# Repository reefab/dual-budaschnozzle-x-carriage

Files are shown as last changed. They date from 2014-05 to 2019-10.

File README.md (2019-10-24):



Dual-Budaschnozzle-X-Carriage
=============================

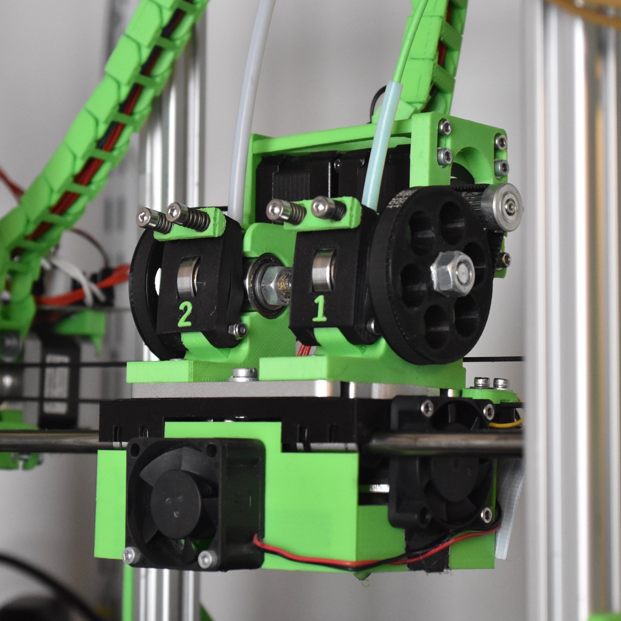
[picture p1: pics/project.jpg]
Assembled

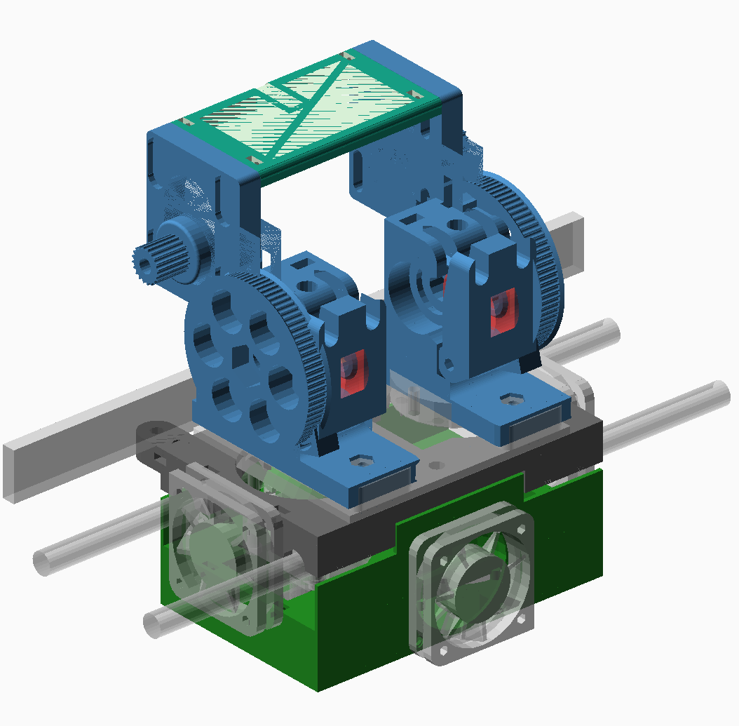
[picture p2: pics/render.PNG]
Final picture


A combination of X-carriage (black), extruders (blue), and fanduct/thermal shield (green) for the [Geetech Dual-head Hotend](http://www.geeetech.com/dualhead-hotend-extruder-0350405mm-nozzle-for-3mm-filament-p-749.html) which uses two budaschnozzles.

Made for Mendel-style horizontal X-axis printers. Has emplacements for four 40mm fans, two on the sides for cooling the buda's radiators and two for cooling the print.

Requires two short (< 33mm tall) nema17 steppers. Designed for 3mm filament but can be changed in the configuration. The beltclamps are designed for a gt2 belt.

Use timing belts instead of a big and small gear.

## Status

Working.

Hundreds of hours of printing have been achieved with this setup, here is some [print results](https://www.flickr.com/photos/reefab_projects/albums/72157651943218993).

## Instructions

### Required Hardware

Beyond the standard hardware you'll need:

 * 4x 40mm fans
 * Aluminum foil tape
 * a [Magic Eraser](https://en.wikipedia.org/wiki/Melamine_foam) (no, really)
 * Kapton tape
 * 2x GT2 pulley 20 teeth, inner diameter 5mm
 * 2x 200mm GT2x6mm belts

As for the hobbed bar, I use two [Hyena v2.0](http://shop.arcol.hu/item/hyena).

### Print
    
 * X-carriage
 * Extruder bodies
 * Extruder idlers
 * Pair of belt clamps
 * Two pairs of gears
 * Fan duct 
 * Extruder bridge

 I printed everything in PLA at 40% infill except for the fanduct that uses 10% infill (and benefit from being printed in ABS).

### X-Carriage

 * On the underside of the x-carriage, glue two M5 nuts and two M3 nuts in their respective nut traps and insert 4-8 zip ties in the lm8uu holders.
 * On the sides of the x-carriage, insert two M3 nuts in side nut catches. Clean the holes before hand if there is any obstructions visible.
 * On the top of the x-carriage, insert 4 M3 nuts in the top nut catches.

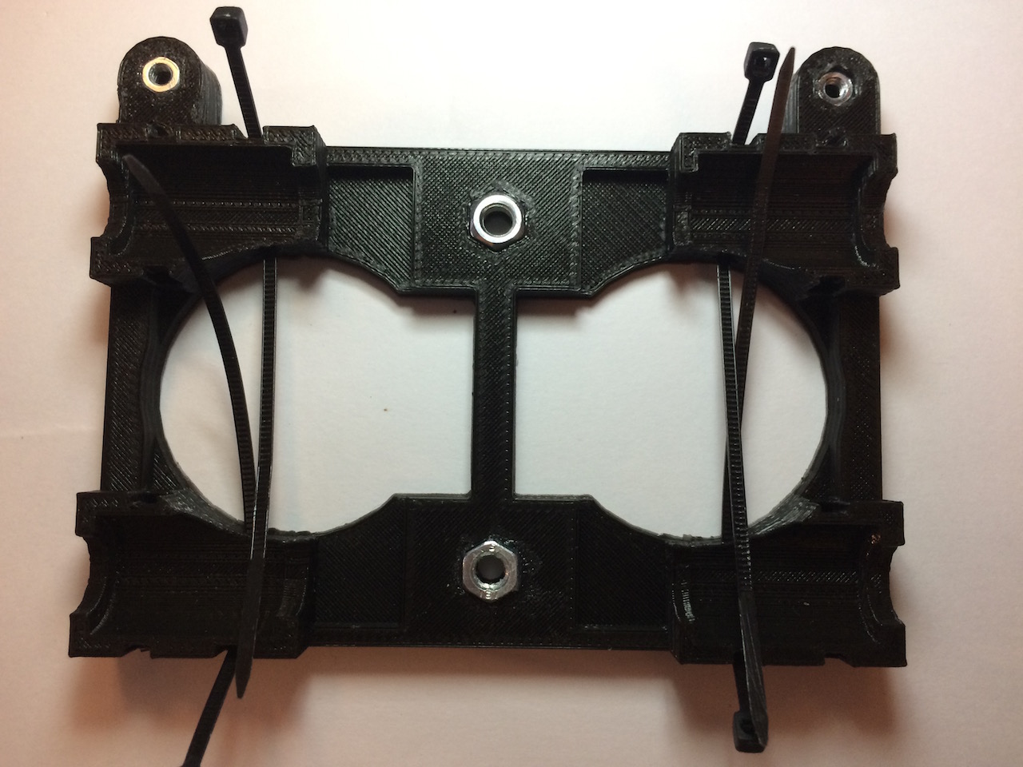
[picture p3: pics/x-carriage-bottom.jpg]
Bottom


**NOTE**: Gluing the bottom nuts is heavily recommended, they will be very difficult to replace without taking the whole assembly apart if they fall.

### Extruders

 * Setup is identical as the [original version](http://www.thingiverse.com/thing:18379)
 * Insert some filament in the extruder so that it sticks through the underside and use that for alignment with the mount plate. Use two M4 screws on each side, flat heads preferably but others may work. Self locking nuts are recommended, or just use two nuts. **The stepper motors should be on the inside**

**NOTE**: Do not over-tighten the m4 nuts, you may need to slide the extruders a bit on the mount plate for the correct alignment.

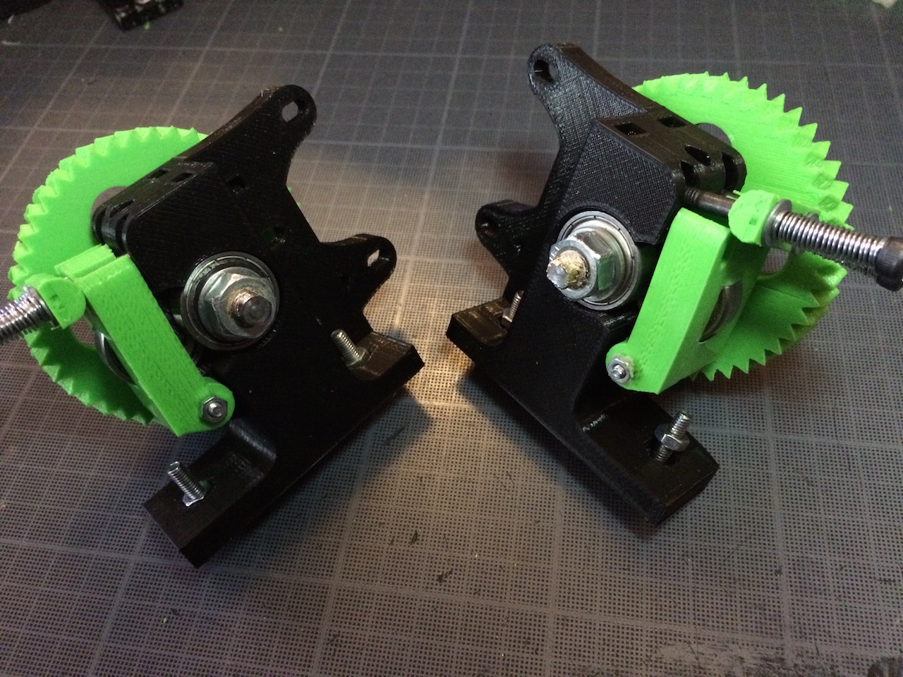
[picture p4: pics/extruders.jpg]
Extruders


### Fanduct/Thermal shield

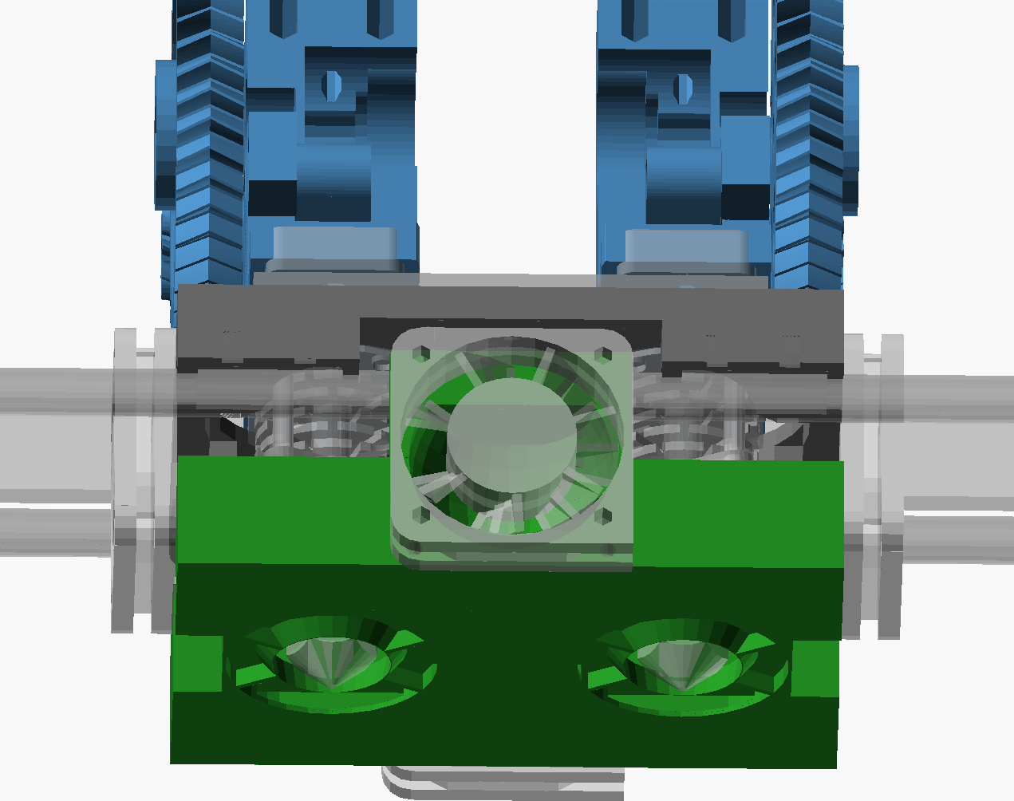
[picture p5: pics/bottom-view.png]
Bottom view


This part has two fans and nozzles to direct cooling air flow on the printed part. It is affixed to the x-carriage using the two side fans used for cooling the fins of the hotends radiators. Dual extrusion printing means that when a particular hotend is not printing, the warm filament will sit still and expand, eventually getting stuck, hence the side fans sitting very close to the radiator fins with directed airflow.

The fanduct directs air to the plastic being extruded as close to the hotend nozzle as possible as it gets the best results in my experience. The airflow also comes from 3 directions to prevent one side getting more cooling that the others as it results in visible artifacts on the printed piece.

Its purpose is also to prevent thermal radiation from the heating block transmitting to the printed part. Those particular hotends have a big heating block that radiates a lot of heat (in part due to their material), cooling only goes so far in remediating that so the best way to prevent the heat from going to the printed piece.

To achieve that, the hotend is almost completely enclosed.

Of course, blocking the heat using the same plastic that the hotend is designed to melt is a bit difficult. To help with that, thermal insulation is required. The main component is [Melamine Foam](https://en.wikipedia.org/wiki/Melamine_foam), it has excellent insulation, will resists the usual temperatures without issues and can be bought in pretty much any supermarkets for a pittance. Ceramic wool might be a better choice, but to stay in the RepRap's spirit, I preferred using widely available materials.

 * On the top of the fanduct, insert 4 M3 nuts in the top nut catches and 4 in the bottom ones
 * Screw in the front and back fans

### Insulation installation

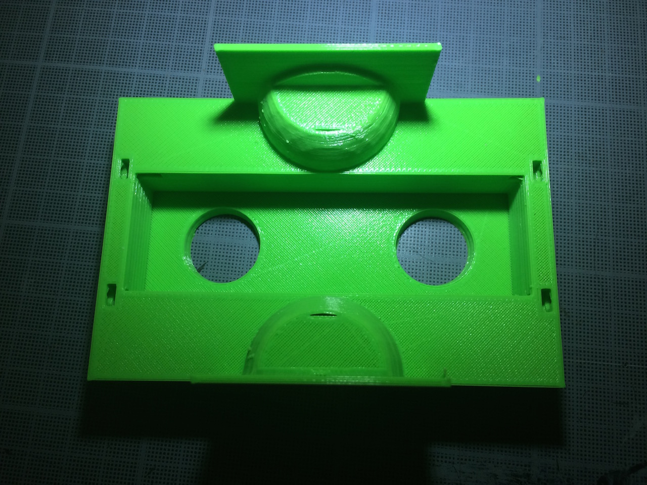
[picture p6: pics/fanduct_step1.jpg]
Step 1

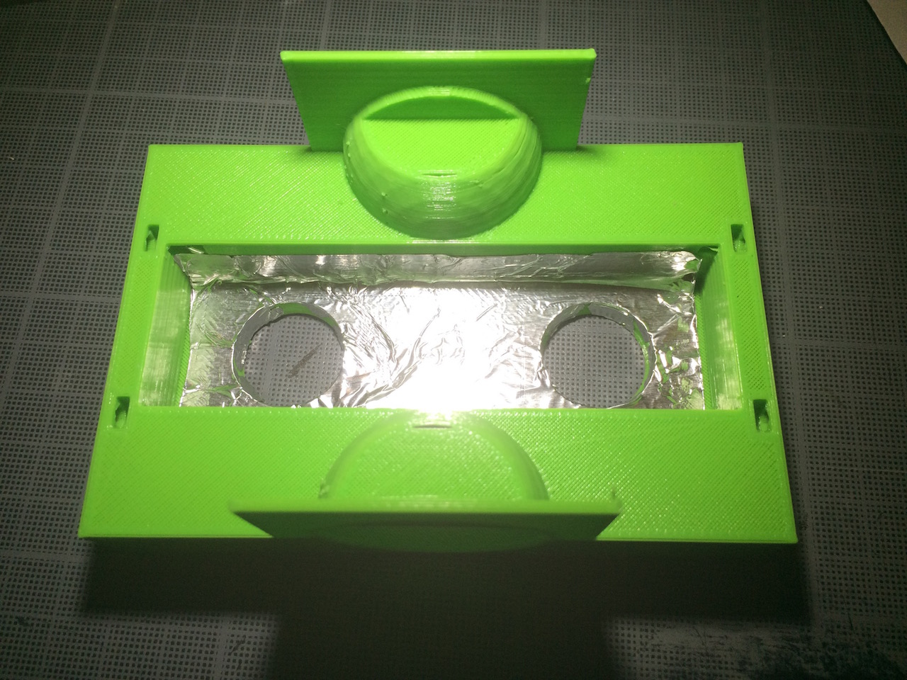
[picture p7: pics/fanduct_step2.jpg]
Step 2
 Apply the foil tape to the inside well and poke holes in it, I used three layers
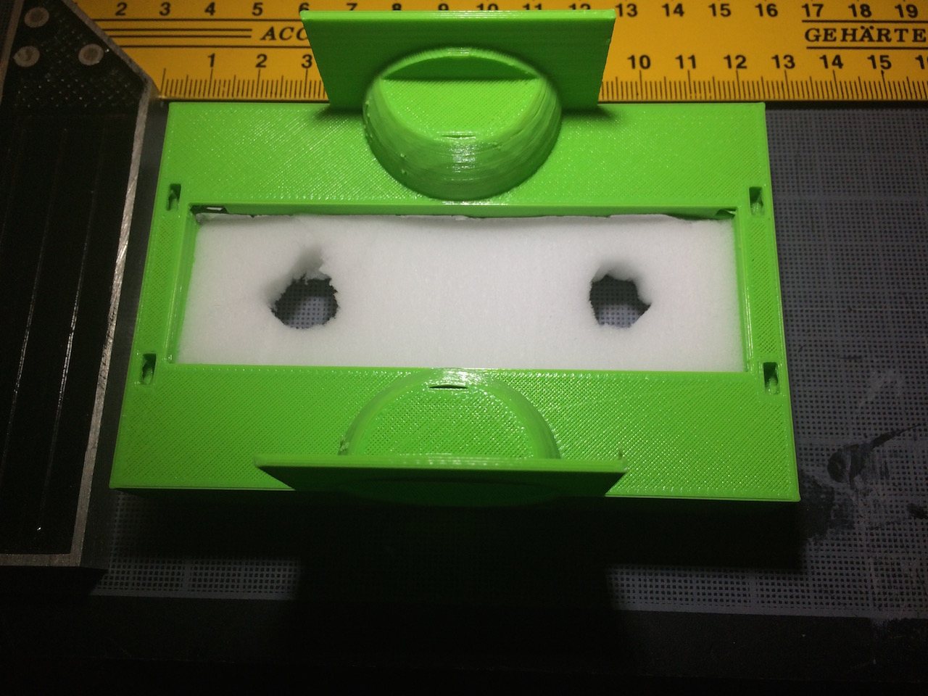
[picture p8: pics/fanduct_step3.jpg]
Step 3
 Cut the Magic Eraser pad to fit inside the well and cut holes. You'll notice that it almost fill the inside of the well but don't worry, it compress very well.
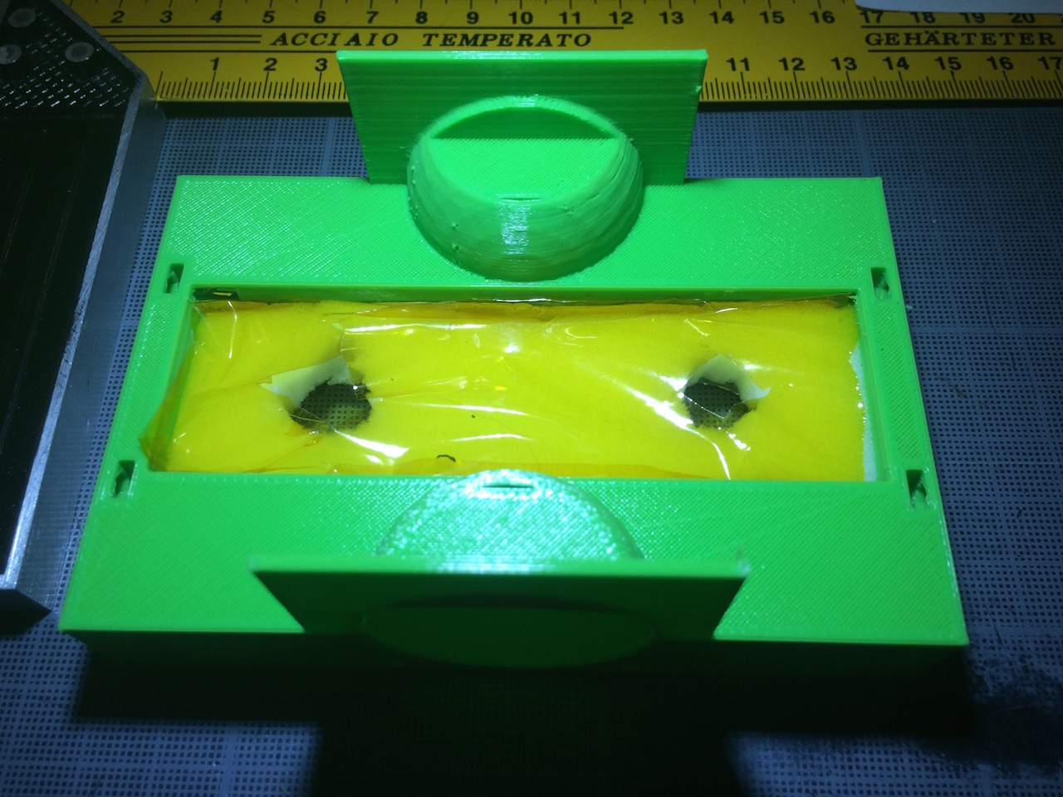
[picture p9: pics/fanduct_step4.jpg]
Step 4
 Put some kapton tape on top of the foam and cut holes

### Final assembly

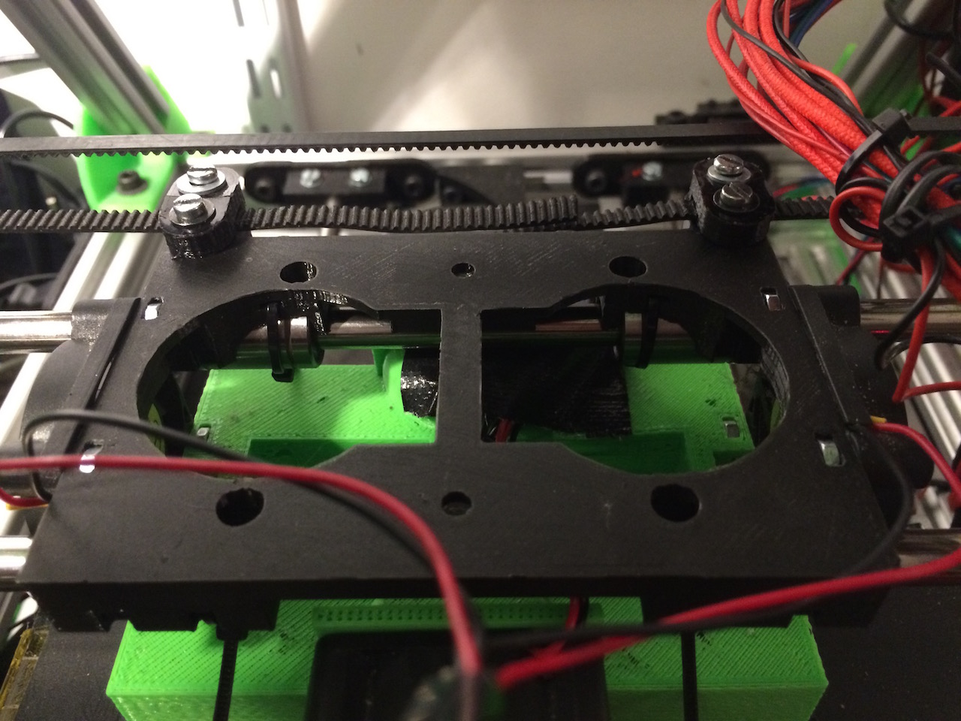
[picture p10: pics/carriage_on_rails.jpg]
Carriage on rails


 * Put the x-carriage on top of the lm8uus on the x-axis rails, secure it with the zip-ties
 * Add the belt clamps on either side and secure them with M3 screws
 * Put the hotends mount plate with the extruders attached on the x-carriage, the M4 bolt's heads should fit in the holes in the x-carriage, if not check for alignment.

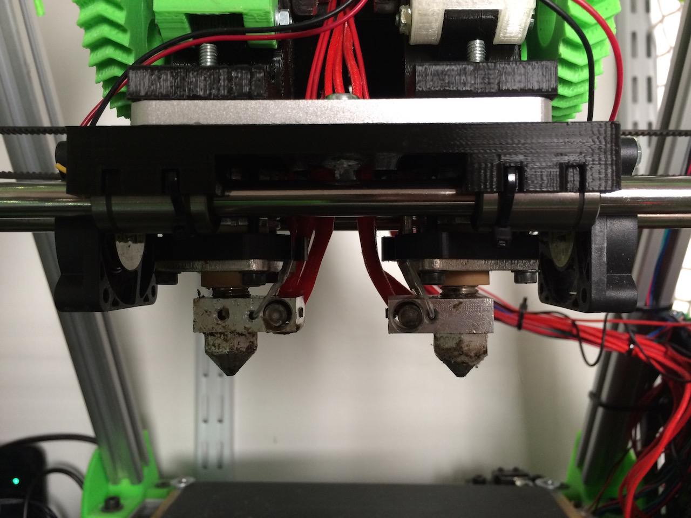
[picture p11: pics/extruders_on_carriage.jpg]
Extruders on carriage


 * Secure it using two short M5 screws using the two central slits on the mount plate
 * Screw in the fans and the fan duct with M3 screws

Assembled

Optional: Glue the includer numbers onto the extruder idlers to identify them.

### Source

 * Extruders: [Greg's Wade reloaded](http://www.thingiverse.com/thing:18379) by jonaskuehling.
 * X-carriage: [Reinforced Prusa X Carriage with Slim LM8UU Holder](http://www.thingiverse.com/thing:18657) by jonaskuehling.

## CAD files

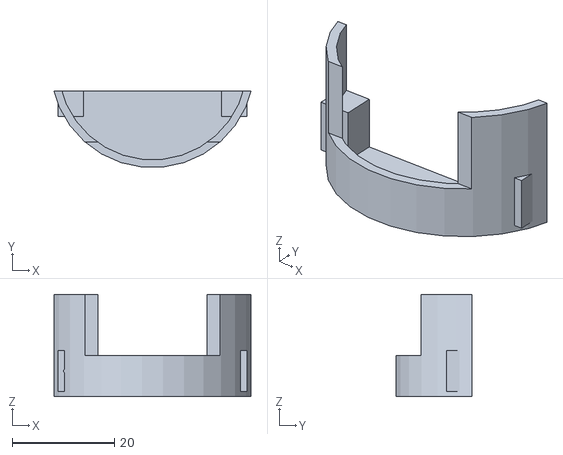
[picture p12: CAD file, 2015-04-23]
dual-budda-fan_duct.stl
38.6 x 14.9 x 20.0

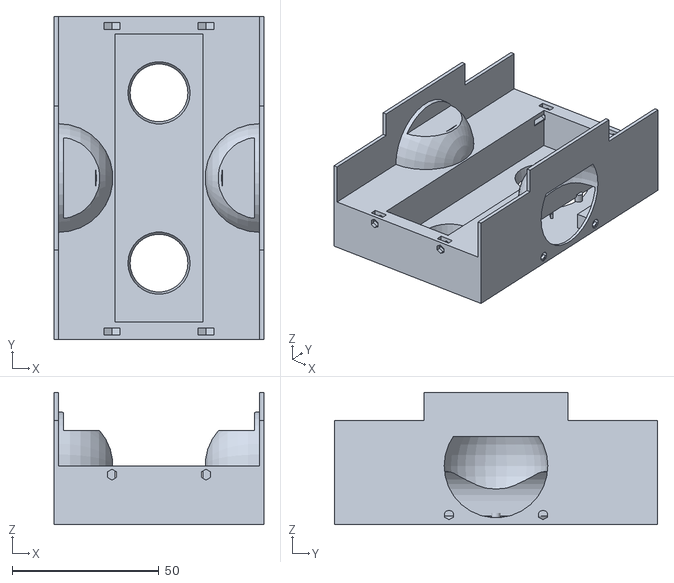
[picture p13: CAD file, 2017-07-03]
output_stl/dual-budda-fanduct.stl
71.4 x 110.0 x 45.0

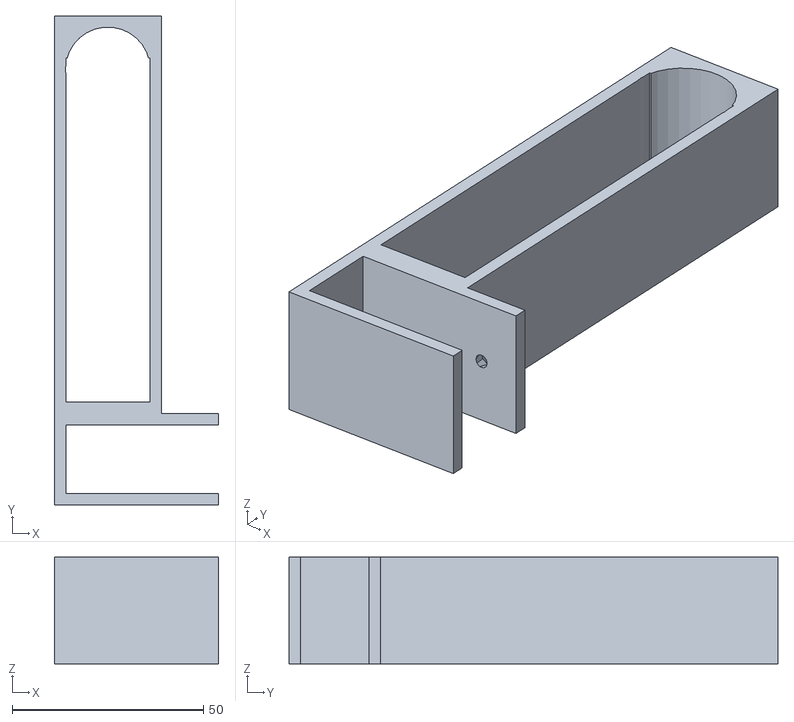
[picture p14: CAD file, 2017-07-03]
src/accessories/rod_holders.stl
43.0 x 128.0 x 28.0

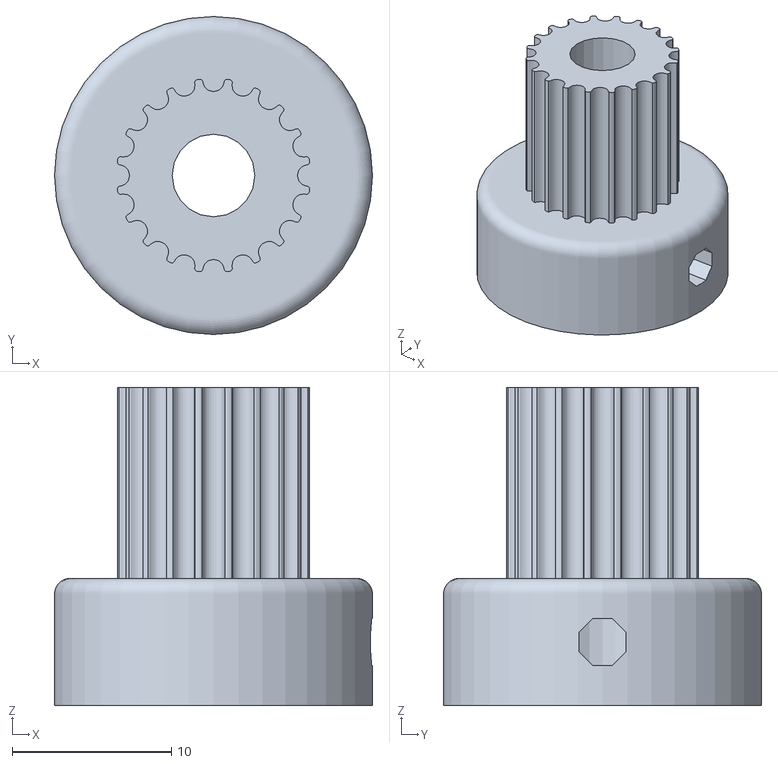
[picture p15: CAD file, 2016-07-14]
src/external_stl/GT2_2mm-20T-OD12.22.stl
20.0 x 20.0 x 20.0

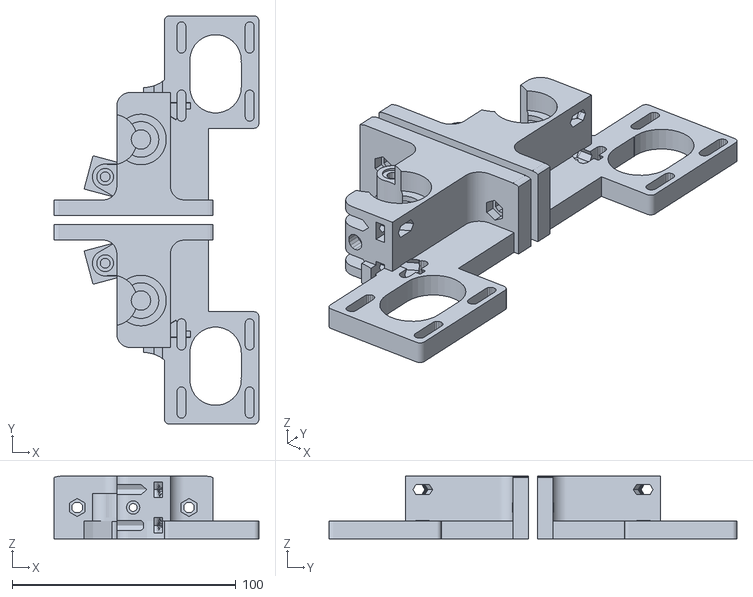
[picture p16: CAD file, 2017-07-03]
output_stl/dual-budda-extruders.stl
91.5 x 182.4 x 28.0

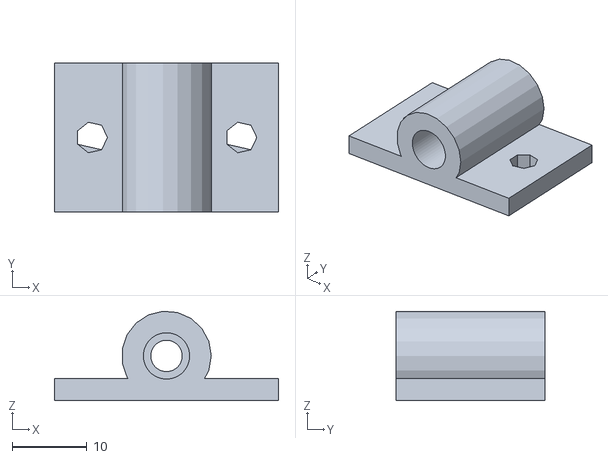
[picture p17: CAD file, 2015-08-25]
src/accessories/feed_tube_holder.stl
30.0 x 20.0 x 12.0

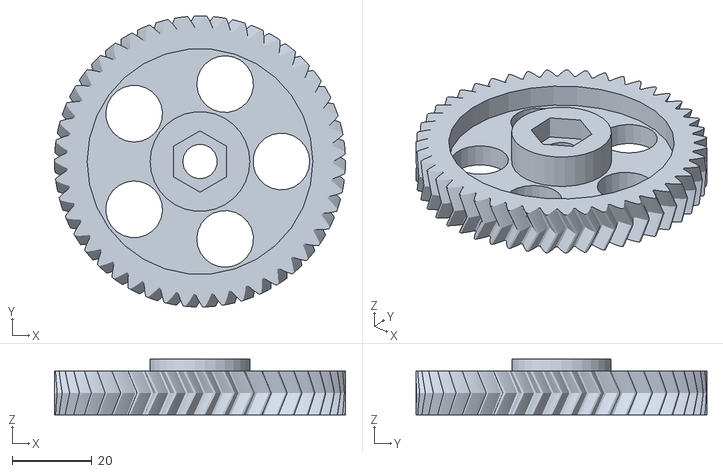
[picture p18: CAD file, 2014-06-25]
src/external_stl/biggearmod_fixed.stl
73.0 x 73.0 x 14.0

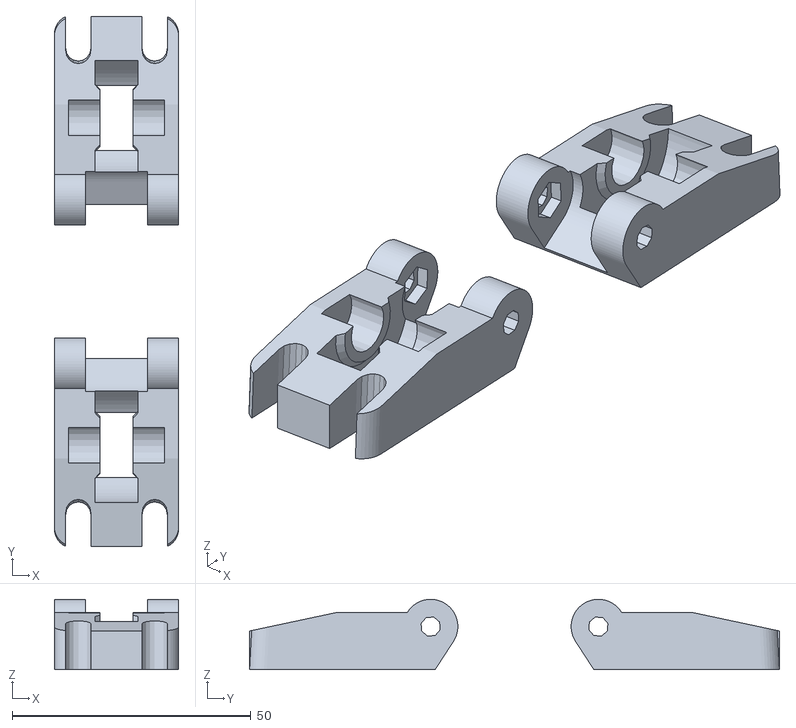
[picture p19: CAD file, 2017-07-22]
stl/idlers.stl
26.0 x 110.9 x 14.7

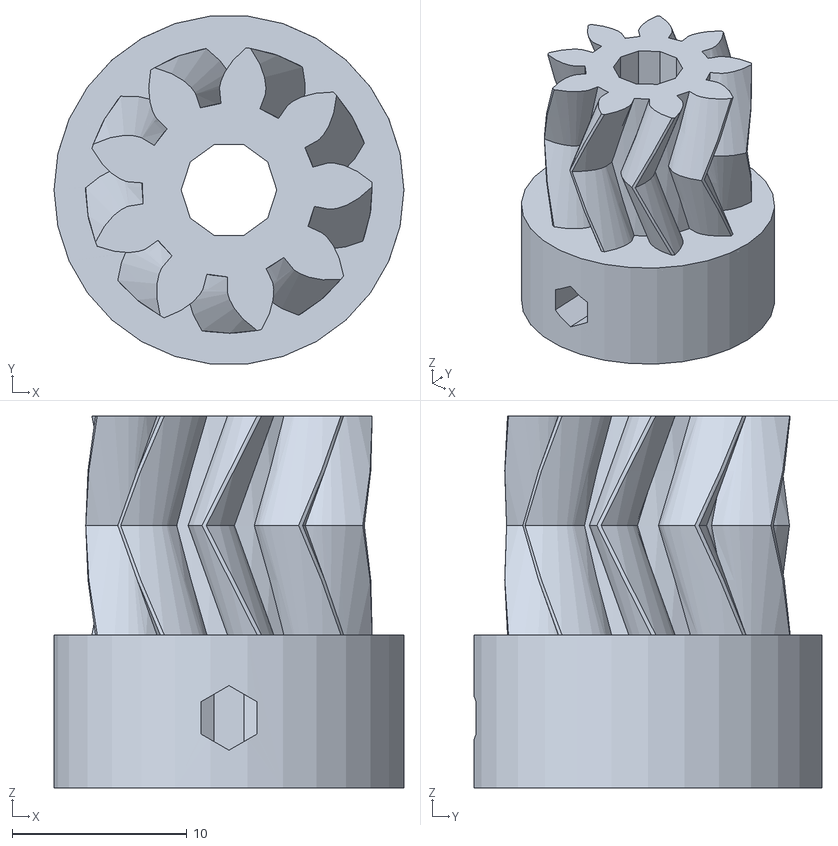
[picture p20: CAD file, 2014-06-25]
src/external_stl/smallgearmod_fixed.stl
20.0 x 19.9 x 21.2

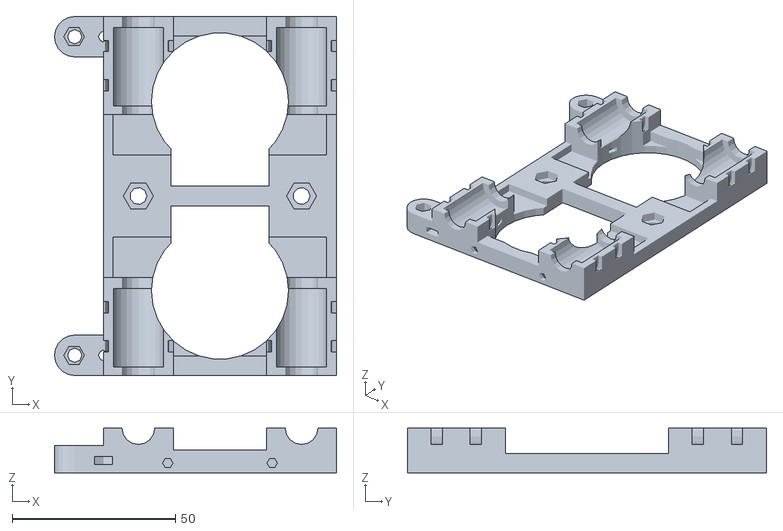
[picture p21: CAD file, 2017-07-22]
stl/xcarriage.stl
86.4 x 110.0 x 13.7

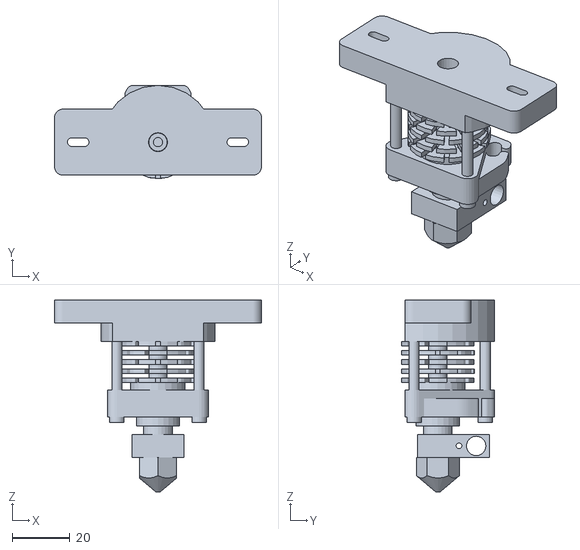
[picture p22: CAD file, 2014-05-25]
src/external_stl/Budaschnozzle.stl
72.0 x 32.4 x 66.8

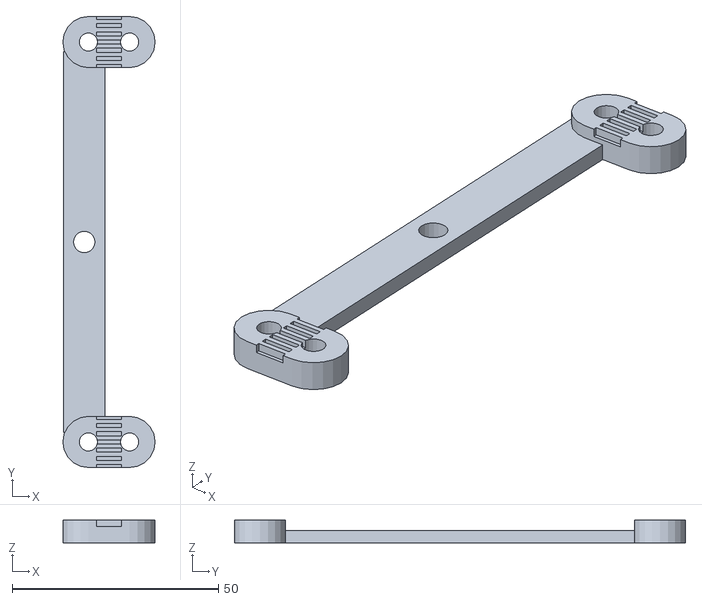
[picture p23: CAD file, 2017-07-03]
output_stl/dual-budda-beltclamps.stl
22.4 x 109.4 x 5.50

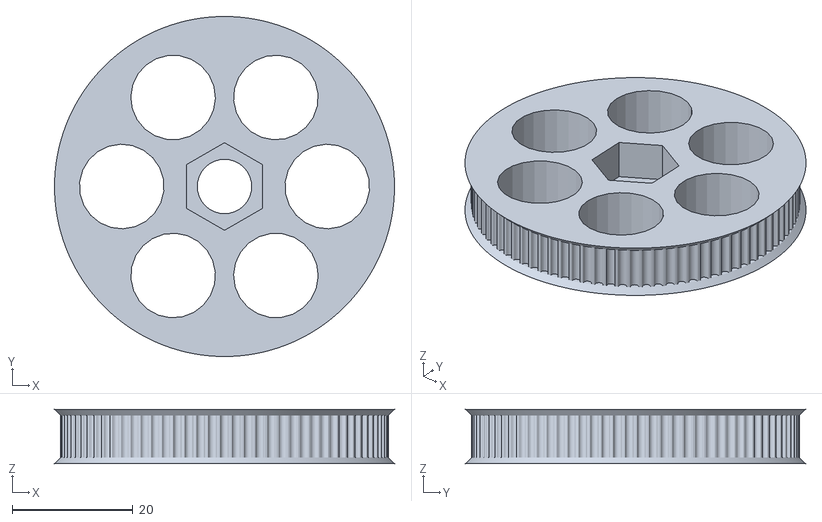
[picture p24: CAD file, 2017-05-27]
output_stl/dual-budda-big_gear_80T.stl
56.2 x 56.2 x 9.00

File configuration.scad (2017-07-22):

// Rendering options
draw_complete = 1;
draw_belt_clamps = 0;
draw_cooling_duct = 0;
draw_extruder= 0;
draw_idler = 0;
draw_carriage = 0;
draw_bridge = 0;
draw_numbers = 0;

variant=0; //0 for metric


vars=[
//[m8_dia, m8_nut, m4_dia, m4_nut, m3_dia, m3_nut, bush_dia, mot_shaft, bush_rod, bush_outerdia, bush_length]
[9,16.4,5,9,4.4,7,11,5.3,8,16,11],//metric
[9,15.7,5.5,10.6,5.5,10.6,11.5,5.3,7.9375,16,11]//SAE
];

//BUSHING TYPE Can generate three versions
// 1 - regular old ones
// 2 - helical ones
// 3 - holders for brass or any other bought bushings
bushing_type = 2;

//Round corner diameter
round_corner_diameter = 8;

//Thin wall size
thin_wall = 3;

//DO NOT TOUCH THIS SECTION!
m8_diameter = vars[variant][0];
m8_nut_diameter = vars[variant][1];
m4_diameter = vars[variant][2];
m4_nut_diameter = vars[variant][3];
m3_diameter = vars[variant][4];
m3_nut_diameter = vars[variant][5];
m3_nut_diameter_bigger = ((m3_nut_diameter  / 2) / cos (180 / 6))*2;
bushing_diameter = vars[variant][6];
motor_shaft=vars[variant][7];
bushing_rodsize = vars[variant][8];
bushing_outerDiameter = vars[variant][9];
bushing_lenght = vars[variant][10];

// X-carriage options

base_length = 110;
rod_dist = 50;

hotends_spacing = 58;
space_width = 30;
fan_hole_spacing = 32;

clearance=0.7;
lm8uu_diameter=15+clearance;
lm8uu_length=24+clearance;
lm8uu_support_thickness=3.2;
lm8uu_end_diameter=m8_diameter+1.5;

lm8uu_holder_width=lm8uu_diameter+2*lm8uu_support_thickness;
lm8uu_holder_length=lm8uu_length+2*lm8uu_support_thickness;
lm8uu_holder_height=lm8uu_diameter*0.75+lm8uu_support_thickness;

lm8uu_holder_gap=(lm8uu_holder_length-6*lm8uu_support_thickness)/2;

screw_hole_r=4/2;

mount_plate_thickness = 5;

belt_loop_height = 18;


// Extruder options

//Set motor- and bolt-elevation for additional clearance when using e.g. 9/47 gears like in http://www.thingiverse.com/thing:11152
elevation=0;

//Set extra gear separation when using slightly bigger non-standard gears like 9/47 herringbone gears
extra_gear_separation=1;

// Nut wrench sizes ISO 4032
m3_wrench = 5.5;
m4_wrench = 6.6;

// Adjust for deeper groove in hobbed bolt, so that idler is still vertical when tightened
// Values like 0.5 to 1 should work, the more, the closer the idler will move to the bolt
// Sometimes the idler will be slightly angled towards the bolt which causes the idler screws
// to slip off the slots in die idler to the top.. Adjusting this should help:
less_idler_bolt_dist = 0;
wade_block_height=55+elevation;
wade_block_width=24;
wade_block_depth=28;

block_bevel_r=6;

wade_base_thickness=7;
wade_base_length=71;
base_leadout=28;

nema17_hole_spacing=1.2*25.4;
nema17_width=1.7*25.4;
nema17_support_d=nema17_width-nema17_hole_spacing;

screw_head_recess_diameter=7.2;
screw_head_recess_depth=2;

motor_mount_rotation=0;
motor_mount_angle=35;
motor_mount_translation=[50.5+extra_gear_separation,34+elevation,0];
motor_mount_thickness=8;
motor_mount_adjust=5;

m8_clearance_hole=8.8;
hole_for_608=22.6;
608_diameter=22;

block_top_right=[wade_block_width,wade_block_height];

layer_thickness=0.2;
filament_feed_hole_d=3.5;
filament_diameter=3;
filament_feed_hole_offset=filament_diameter + 0.5;
idler_nut_trap_depth=7.3;
idler_nut_thickness=3.7;

gear_separation=7.4444+32.0111+0.25+extra_gear_separation;

ptfe_tube_dia = 6.5;

extruder_color = "SteelBlue";
carriage_color = "DimGray";
fanduct_color = "ForestGreen";

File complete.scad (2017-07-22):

// Main configuration file
include <configuration.scad>

include <src/x-carriage/LM8UU_holder_ziptie.scad>

include <src/nutsnbolts/cyl_head_bolt.scad>

// Fan module, for display only
include <src/x-carriage/fan.scad>

include <src/x-carriage/carriage.scad>
include <src/x-carriage/belt_clamp.scad>
include <src/fanduct/fanduct.scad>
include <src/extruder/extruder.scad>
include <src/extruder/bridge.scad>

if (draw_complete == 1) {
    rotate([0, 180, 0]) color(carriage_color) simonkuehling_x_carriage();
    rotate([0, 180, 0]) % mount_plate();
    // side fans
    for (i=[-1,1])
        translate([0, i* (base_length/2 + 5), -18])
            rotate([0, 90, 90]) % fan(40,10.2);
    // Rods
    for (i=[-1,1])
        translate([rod_dist / 2* i, 0, -(LM8UU_dia/2+body_wall_thickness+4)])
            rotate([90,0,0])
            % cylinder(h=base_length*2,r=4,$fs=1,center=true);

    // Belt
    translate([40, 0, belt_loop_height/2])
        % cube([5, base_length * 2, belt_loop_height], center=true);

    // Front/back fans
    for (i=[-1,1])
        translate([i* (rod_dist/2 + body_width/2 + 5), 0, -33])
            rotate([0, -90, 0]) % fan(40,10.2);
    // Fanduct
    rotate([0, 180, 0]) translate([0,0,42]) color(fanduct_color) cooling_duct();

    // extruders
    extruder_offset = -7.5;
    translate([extruder_offset, hotends_spacing/2 + wade_block_depth/2 , mount_plate_thickness])
        rotate([90, 0, 0])
            color(extruder_color) wade(hotend_mount=groovemount, legacy_mount=false);
    translate([extruder_offset, -hotends_spacing/2 - wade_block_depth/2 , mount_plate_thickness])
        rotate([90, 0, 0])
            mirror([0, 0, 1])
                color(extruder_color) wade(hotend_mount=groovemount, legacy_mount=false);
    // extruders idlers
    translate([extruder_offset, hotends_spacing/2 + wade_block_depth/2 , mount_plate_thickness])
        rotate([90, 0, 0])
            color(extruder_color) wadeidler();
    translate([extruder_offset, -hotends_spacing/2 - wade_block_depth/2 , mount_plate_thickness])
        rotate([90, 0, 0])
            mirror([0, 0, 1])
                color(extruder_color) wadeidler();

    // Extruder bridge
    translate([15, -35, 89.1]) bridge();

}

if (draw_carriage == 1 && draw_complete == 0) {
    simonkuehling_x_carriage();
}

if (draw_belt_clamps == 1 && draw_complete == 0) {
    translate([-6, 0, 0]) difference() {
        translate([0, 0, 1.5]) cube([10, 92.5, 3], center=true);
        cylinder(d=5.2, h=4, $fn=20);
    }
    for (i=[-1,1])
        translate([0,i*(48.5),0])
            belt_clamp();
}

if (draw_cooling_duct == 1 && draw_complete == 0) {
    rotate([180, 0, 0]) cooling_duct();
}

if (draw_extruder == 1 && draw_complete == 0) {
    translate([30, 2, 0]) wade(hotend_mount=groovemount, legacy_mount=false);
    translate([30, -2, 0]) mirror([0, 1, 0]) wade(hotend_mount=groovemount, legacy_mount=false);
}

if (draw_idler == 1 && draw_complete == 0) {
    rotate([0,-90,0])
        wadeidler();
    mirror ([0, 1, 0])
        rotate([0,-90,0])
            wadeidler();
}

if (draw_bridge == 1 && draw_complete == 0) {
    bridge();
}

if (draw_numbers == 1 && draw_complete == 0) {
    linear_extrude(1) text("1", size=8);
    translate([10, 0, 0]) linear_extrude(1) text("2", size=8);
}

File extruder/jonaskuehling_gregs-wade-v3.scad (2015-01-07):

// Greg's Wade Extruder. 
// It is licensed under the Creative Commons - GNU GPL license. 
//  2010 by GregFrost
// Extruder based on prusa git repo.
// http://www.thingiverse.com/thing:6713

include<configuration.scad>
include<jonaskuehling-default.scad>

// Define the hotend_mounting style you want by specifying hotend_mount=style1+style2 etc.
malcolm_hotend_mount=1;
groovemount=2;
peek_reprapsource_mount=4;
arcol_mount=8;
mendel_parts_v6_mount=16; 
grrf_peek_mount=32;
wildseyed_mount=64;
geared_extruder_nozzle=128; // http://reprap.org/wiki/Geared_extruder_nozzle
jhead_mount=256;
reprapfaborg_mount=512; // http://reprap-fab.org hotend with 10mm PEEK insulator

//Set the hotend_mount to the sum of the hotends that you want the extruder to support:
//e.g. wade(hotend_mount=groovemount+peek_reprapsource_mount);

//Set motor- and bolt-elevation for additional clearance when using e.g. 9/47 gears like in http://www.thingiverse.com/thing:11152
elevation=10;

//Set extra gear separation when using slightly bigger non-standard gears like 9/47 herringbone gears
extra_gear_separation=2;

// Nut wrench sizes ISO 4032
m3_wrench = 5.5;
m4_wrench = 7;

// Adjust for deeper groove in hobbed bolt, so that idler is still vertical when tightened
// Values like 0.5 to 1 should work, the more, the closer the idler will move to the bolt
// Sometimes the idler will be slightly angled towards the bolt which causes the idler screws
// to slip off the slots in die idler to the top.. Adjusting this should help:
less_idler_bolt_dist = 0;



draw_extruder = 1;
draw_idler = 0;

////////// RENDER EXTRUDER //////////////////////////////////////////////////////////////
if (draw_extruder == 1) {
    translate([30, 2, 0]) wade(hotend_mount=groovemount, legacy_mount=false);
    translate([30, -2, 0]) mirror([0, 1, 0]) wade(hotend_mount=groovemount, legacy_mount=false);
    translate([41, 46, 0]) rotate([180, 0 ,105]) % import("biggearmod_fixed.stl");
}
//wade(hotend_mount=reprapfaborg_mount, legacy_mount=false);
//wade(hotend_mount=jhead_mount, legacy_mount=false);
//wade(hotend_mount=arcol_mount, legacy_mount=false);
//wade(hotend_mount=grrf_peek_mount, legacy_mount=false);


////////// RENDER BEARING WASHER ///////////////////////////////////////////////////
/*translate([-15,45,0])*/
/*	bearing_washer();*/


////////// RENDER IDLER /////////////////////////////////////////////////////////////////////
if (draw_idler == 1) {
    rotate([0,-90,0])
    	wadeidler();
    mirror ([0, 1, 0])
        rotate([0,-90,0])
            wadeidler();
}

/**
 * Extruder
 * @name Extruder
 * @assembled
 * @using 1 small-gear
 * @id extruder
 * @using 1 idler
 * @using 1 extruder-body
 * @using 1 m3nut
 * @using 1 m3washer
 * @using 1 m3x25
 * @step Take idler and insert nut into small nut-trap inside the hinge.
 * @step While holding the nut in place, preprare M3x25 bolt with washer and screw it into the hinge just enough to hold the nut.
 * @step Now take the extruder body and idler. Place idler on the hinge counterpart and compleately screw the M3x25 bolt. This will create secured hinge.
 * 
 * @using 2 m4nut
 * @step Place M4 nuts into their nut traps, secure them with piece of tape. We need them in place, since later they would be harder to access.
 * 
 * @using 3 m3x10
 * @using 3 m3washer
 * @using 1 NEMA17
 * @step Prepare your NEMA17 stepper motor and three M3x10 screws with washers.
 * @step Hold motor on place and lightly tighten the screws. We need to adjust motor position later, no need to tighten it hard.
 * 
 * @using 1 large-gear
 * @using 1 m8washer
 * @using 2 m8nut
 * @using 2 bearing-608
 * @step Place two skate bearings on ther position, they should snuggly fit in.
 * @step Insert prepared large gear into the body with mounted bearings.
 * @step Check if the alignment of hobbed part with the filament path. Adjust it accordingly with adding or removing M8 washers.
 * @step After adjusting, we need to fix the bolt in. So we place washer at the end of hobbed bolt and with two M8 nuts we will do locknut by tightening them against each other.
 * @step Check if large gear turns freely.
 * 
 * @using 2 m3x40
 * @using 4 m3washer
 * @using 2 extruder-spring
 * @step Prepare two M3x40 screws with sandwitch of washer-spring-washer.
 * @step Insert two M3 nuts into nut traps on top of drive mechanism. [[extruder/top-nut-traps.png]]
 * @step Insert prepared screws into the holes on idler. Close the idler and tighten the screws into the trapped nuts. More you tighten those screws, more pressure will be on fillament.
 * @step Your extruder is done. [[extruder/assembled.jpg]]
 */

/**
 * Extruder body
 * @name Extruder body
 * @category Printed
 * @id extruder-body
 */

/**
 * Extruder idler
 * @name Extruder Idler
 * @id idler
 * @category Printed
 * @using 1 bearing-608
 * @using 1 idler-m8-piece
 * @step Insert piece of M8 rod into bearing.
 * @step Insert 608 bearing with rod into printed idler part.
 */

/**
 * Small M8 rod 
 * @name Idler
 * @id idler-m8-piece
 * @category Rods and Bars
 */

/**
 * Spring used for idler on extruder.
 * @name Extruder spring
 * @id extruder-spring
 */

//===================================================
// Parameters defining the wade body:
wade_block_height=55+elevation;
wade_block_width=24;
wade_block_depth=28;

block_bevel_r=6;

base_thickness=7;
base_length=70;
base_leadout=25;

nema17_hole_spacing=1.2*25.4; 
nema17_width=1.7*25.4;
nema17_support_d=nema17_width-nema17_hole_spacing;

screw_head_recess_diameter=7.2;
screw_head_recess_depth=3;

motor_mount_rotation=25;
motor_mount_translation=[50.5+extra_gear_separation,34+elevation,0];
motor_mount_thickness=8;

m8_clearance_hole=8.8;
hole_for_608=22.6;
608_diameter=22;

block_top_right=[wade_block_width,wade_block_height];

layer_thickness=0.2;
filament_feed_hole_d=3.5;
filament_diameter=3;
filament_feed_hole_offset=filament_diameter+1.5;
idler_nut_trap_depth=7.3;
idler_nut_thickness=3.7;

gear_separation=7.4444+32.0111+0.25+extra_gear_separation;

function motor_hole(hole)=[motor_mount_translation[0],motor_mount_translation[1]] +
	rotated(45+motor_mount_rotation+hole*90)*nema17_hole_spacing/sqrt(2);

// Parameters defining the idler.

filament_pinch=[
	motor_mount_translation[0]-gear_separation-filament_feed_hole_offset-filament_diameter/2,
	motor_mount_translation[1],
	wade_block_depth/2];
idler_axis=filament_pinch-[608_diameter/2,0,0];
idler_fulcrum_offset=608_diameter/2+3.5+m3_diameter/2;
idler_fulcrum=idler_axis-[0+less_idler_bolt_dist,idler_fulcrum_offset,0];
idler_corners_radius=4; 
idler_height=12;
idler_608_diameter=608_diameter+2;
idler_608_height=9;
idler_mounting_hole_across=8;
idler_mounting_hole_up=15;
idler_short_side=wade_block_depth-2;
idler_hinge_r=m3_diameter/2+3.5;
idler_hinge_width=6.5;
idler_end_length=(idler_height-2)+5;
idler_mounting_hole_diameter=m4_diameter+0.25;
idler_mounting_hole_elongation=0.9;
idler_long_top=idler_mounting_hole_up+idler_mounting_hole_diameter/2+idler_mounting_hole_elongation+2.5;
idler_long_bottom=idler_fulcrum_offset;
idler_long_side=idler_long_top+idler_long_bottom;

module bearing_washer(){
	difference(){
		cylinder(r=hole_for_608/2-0.3,h=1);
		translate([0,0,-1])
		cylinder(r=8,h=3);
	}
}

module wade (hotend_mount=0,legacy_mount=false){
	difference (){
		union(){
			// The wade block.
			cube([wade_block_width,wade_block_height,wade_block_depth]);

			// Filler between wade block and motor mount.
			translate([10,motor_mount_translation[1]-hole_for_608/2-elevation,0])
			cube([wade_block_width+extra_gear_separation + 4,
				wade_block_height-motor_mount_translation[1]+hole_for_608/2+elevation,
				motor_mount_thickness]);

			// Connect block to top of motor mount.
			linear_extrude(height=motor_mount_thickness)
			barbell(block_top_right-[0,5],motor_hole(0),5,nema17_support_d/2,100,60);

			//Connect motor mount to base.
			linear_extrude(height=motor_mount_thickness)
			barbell([base_length/1.5-base_leadout,
				base_thickness/2],motor_hole(2),base_thickness/2,
				nema17_support_d/2,100,60);

			// Round the ends of the base
			translate([base_length-base_leadout,base_thickness/2,0])
			cylinder(r=base_thickness/2,h=wade_block_depth,$fn=20);

			translate([-base_leadout,base_thickness/2,0])
			cylinder(r=base_thickness/2,h=wade_block_depth,$fn=20);

			//Provide the bevel betweeen the base and the wade block.
			render()
			difference(){
				translate([-block_bevel_r,0,0])
				cube([block_bevel_r*2+wade_block_width,
					base_thickness+block_bevel_r,wade_block_depth]);				
				translate([-block_bevel_r,block_bevel_r+base_thickness])
				cylinder(r=block_bevel_r,h=wade_block_depth,$fn=60);
				translate([wade_block_width+block_bevel_r,
					block_bevel_r+base_thickness])
				cylinder(r=block_bevel_r,h=wade_block_depth,$fn=60);
			}
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

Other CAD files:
stl/fanduct.stl
output_stl/dual-budda-idlers.stl
output_stl/dual-budda-xcarriage.stl
stl/extruders.stl
stl/beltclamps.stl
x-carriage/configuration.scad
src/accessories/feed_tube_holder.scad
src/accessories/rod_holders.scad
src/extruder/bridge.scad
src/extruder/extruder.scad
src/extruder/functions.scad
src/extruder/gregs-wadebits.scad
src/extruder/jonaskuehling-default.scad
src/extruder/metric.scad
src/fanduct/fanduct.scad
src/gear/80T_gt2.scad
src/x-carriage/LM8UU_holder_ziptie.scad
src/x-carriage/belt_clamp.scad
src/x-carriage/carriage.scad
src/x-carriage/fan.scad
stl/big_gear_80T.stl
stl/bridge.stl
stl/numbers.stl
x-carriage/carriage.scad

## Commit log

2014-05-25 Makefile for generating stl file and image preview
    [dual-budda-xcarriage.stl, jonaskuehling_x-carriage_lm8uu.scad]
2014-05-25 Shrinked it a bit
    [jonaskuehling_x-carriage_lm8uu.scad]
2014-05-25 Added buddashnozzle stl for testing
    [Budaschnozzle.stl, jonaskuehling_x-carriage_lm8uu.scad]
2014-05-25 Removed one lm8uu holder and moved one to the center
    [dual-budda-xcarriage.stl, jonaskuehling_x-carriage_lm8uu.scad]
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2014-06-09 Corrected hole between hotends
    [jonaskuehling_x-carriage_lm8uu.scad]
2014-06-09 Added front fan mount
    [jonaskuehling_x-carriage_lm8uu.scad]
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2014-06-25 Added extruder and moved things around
    [Budaschnozzle.stl, big-gear-mod_SAE.stl, biggearmod_fixed.stl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]
2014-06-25 Removed extraneous STL files.
    [big-gear-mod_SAE.stl, dual-budda-xcarriage.stl, extru.stl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]
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2014-07-03 added mount plate clamps
    [dual-budda-beltclamps.stl, dual-budda-plate_clamps.stl, dual-budda-xcarriage.stl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]
2014-07-03 corrected slight mistake: removed belt clamps from carriage
    [dual-budda-beltclamps.stl, dual-budda-xcarriage.stl, jonaskuehling_x-carriage_lm8uu.scad]
2014-07-03 Flipped the plate clamps around
    [dual-budda-plate_clamps.stl, dual-budda-xcarriage.stl, jonaskuehling_x-carriage_lm8uu.scad]
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2014-12-31 Display the two rods and put back the 4 lm8uu holders at the corners of the carriage
    [jonaskuehling_x-carriage_lm8uu.scad]
2015-01-04 Changed lm8uu holders to zipped ones
    [40mm_Fan_Shroud.stl, LM8UU_holder_ziptie.scad, jonaskuehling_x-carriage_lm8uu.scad]
2015-01-05 Moved fans to the side, removed front fan holes, double latches holes and reduced central spacing
    [jonaskuehling_x-carriage_lm8uu.scad]
2015-01-05 Added nutsnbolts library and central mounting holes nuttrap
    [jonaskuehling_x-carriage_lm8uu.scad]
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2015-01-06 Added nut trap for belt clamp
    [jonaskuehling_x-carriage_lm8uu.scad]
2015-01-06 Side fan nut traps
    [jonaskuehling_x-carriage_lm8uu.scad]
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2015-01-06 rear fan duct holes and traps
    [jonaskuehling_x-carriage_lm8uu.scad]
2015-01-06 Fixed belt clamp hole
    [jonaskuehling_x-carriage_lm8uu.scad, lm8uu-holder-slim.scad]
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2015-01-06 lowered rest fan duct holes to prevents nut interfering with mounting plate
    [jonaskuehling_x-carriage_lm8uu.scad]
2015-01-07 Fixed belt clamp sockets interfering with zip ties channels
    [jonaskuehling_x-carriage_lm8uu.scad]
2015-01-07 Added nut trap to exterior belt clamp socket holes
    [jonaskuehling_x-carriage_lm8uu.scad]
2015-01-07 Widened slightly the hotend holes
    [jonaskuehling_x-carriage_lm8uu.scad]
2015-01-07 Added big gear display to extruder to check alignement
    [jonaskuehling_gregs-wade-v3.scad]
2015-01-07 Fixed filament feed hole not going through all the way
    [jonaskuehling_gregs-wade-v3.scad]
2015-01-07 Added more support to the motor mount
    [jonaskuehling_gregs-wade-v3.scad]
2015-01-07 Updated STL files for release
    [dual-budda-extruders.stl, dual-budda-idlers.stl, dual-budda-xcarriage.stl]
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2015-04-23 thicker walls for fan duct
    [dual-budda-fan_duct.stl, jonaskuehling_x-carriage_lm8uu.scad]
2015-04-29 Started work on the rear fanduct
    [jonaskuehling_x-carriage_lm8uu.scad]
2015-04-29 main plate of rear fan duct
    [jonaskuehling_x-carriage_lm8uu.scad]
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2015-04-30 tweaked funnels to make sure they stay at a constant thickness
    [funnel.scad]
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2015-05-04 Fan duct tested and functional.
    [jonaskuehling_x-carriage_lm8uu.scad]
2015-05-04 Reorganized files and modules
    [belt_clamp.scad, carriage.scad, dual-budda-beltclamps.stl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]
2015-05-04 Release with new rear fan duct
    [dual-budda-beltclamps.stl, dual-budda-extruders.stl, dual-budda-idlers.stl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]
2015-05-05 Reverted to an older version of the carriage STL due to an OpenSCAD bug that caused an incorrect manifold error
    [dual-budda-xcarriage.stl]
2015-05-22 Made rear fanduct mounting holes slits for adjusting
    [rear_fanduct.scad]
2015-05-22 changed nozzles for better airflow direction
    [rear_fanduct.scad]
2015-05-31 Fanduct V3 with bigger nozzles
    [rear_fanduct.scad]
2015-05-31 Redoing then fanducts in one piece and from scratch
    [cooling.scad, main.scad]
2015-05-31 Cooling duct main body
    [cooling.scad]
2015-06-01 Pipe module, to divert airflow
    [cooling.scad]
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2015-06-01 Fanduct holes way closer to the hotend nozzle
    [cooling.scad]
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2015-06-02 Removed plastic in unused parts
    [cooling.scad, dual-budda-cooling_duct.stl]
2015-06-02 baffles added to the nozzles exit
    [cooling.scad, dual-budda-cooling_duct.stl]
2015-08-23 Re-organizing files to move configuration to a main file
    [carriage.scad, complete.scad, dual-budda-rear_fanduct.stl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]
2015-08-23 Added extruders to complete file
    [Budaschnozzle.stl, LM8UU_holder_ziptie.scad, belt_clamp.scad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]
2015-08-23 Changed nutsnbolts library location
    [complete.scad]
2015-08-23 Converted tabs to spaces
    [extruder.scad]
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2015-08-23 Moved more configuration values inside its own file
    [complete.scad, configuration.scad]
2015-08-23 Fix: forgot to put wells for the extruder's top nut traps
    [complete.scad, configuration.scad, dual-budda-extruders.stl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]
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2015-08-25 Added accessories
    * feed tube holder
    * rod holder, for the filament spools
    [feed_tube_holder.scad, feed_tube_holder.stl, rod_holders.scad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]
2015-08-27 Modified idlers and moved filament feed closer to the hobbed bolt for better grip
    [carriage.scad, complete.scad, configuration.scad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]
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2015-08-31 Hotends now have a central trench to fit into instead of separate holes
    [fanduct.scad]
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2015-09-14 Added support pillars to fanduct for easier printing
    [dual-budda-fanduct.stl, fanduct.scad]
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2016-07-14 replace gears with a gt2 belt
    [80T_gt2.scad, configuration.scad, extruder.scad]
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2016-07-14 TEMP: replacing the small gear with a gt2 pulley stl for display only
    [GT2_2mm-20T-OD12.22.stl, extruder.scad]
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2017-02-12 Tweaked belted pulley for tighter tolerances
    [80T_gt2.scad]
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2017-02-15 Added an option to change the angle between the hobbed bolt and the motor
    [configuration.scad, extruder.scad]
2017-02-15 changed motor mount angle and added hole for motor
    [configuration.scad, extruder.scad]
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2017-05-27 Thickened motor mounts and made adjustable mounts vertical
    [configuration.scad, extruder.scad]
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
